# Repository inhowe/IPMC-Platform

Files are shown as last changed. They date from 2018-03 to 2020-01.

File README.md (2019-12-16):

# IPMC测控平台-NUAA-IBSS

版本索取API：https://api.github.com/repos/drinow/IPMC-Platform/releases/latest

## 更新日志
- 20191216更新
  - 发现BUG，关闭了采样率调整功能
  - 输出电流过大时，系统执行自动复位
- 20190515更新
	- 现在可以在升级前知道新版本具体更新了哪些东西
	- 新增分隔显示的曲线图
	- 控制功能统一移入到选项卡中
	- 完善上位机和下位机的功率控制算法，现已支持功率补偿
	- 其他细节优化，使逻辑性更加统一，结构更加高效
- 20190513更新
	- 增大曲线能够存储的点数（400W点）
	- 给XY图增加一个使能开关，默认关闭
- 20190509更新
	- 新增更新控制参数按钮
- 20190506更新
	- 上位机降低XY图的数据量，新增"清空XY图"按键，现在因XY图数据量过大出现卡顿现象的概率更低了
	- 上位机修改了"使能控制"按钮逻辑，你的每一次操作都能被正确反映
	- 上位机现在支持访问github从而下载完整工程了
	- 下位机新增IIR、RC滤波器，信号噪声现得到了有效抑制
	- 其他的细节优化
- 20190412更新
    - 上位机新增电路原理图、BOM单等资料
    - 测控板新增独立看门狗程序
- 20190406更新
    - 新增许多说明资料以及TIPS提示框
    - 修改了更新URL
    - 新增LICENCE
    - 其他优化
- 20190316更新
    - 新增PID等控制功能
    - 界面降级并优化
    - 细节修复
- 20190305更新
    - 新增PID控制、BangBang控制功能及界面
    - BUG修复
    - 新增协议，包括支持开关DEBUG模式、开关控制模式、系统复位等功能
    - 过流、过压等超量程指示灯改为红色
- 20180915更新
	- 修改界面为NXP风格（需要使用最新的LabView驱动）
- 20180912更新
	- 新增XY图
	- 新增提示消息
	- 新增一些功能开关
	- 优化部分逻辑
- 20180714更新
	- 提高串口速率至460800，提高采样率至10ms；
	- 修改上位机相应解析代码；
	- 替换掉RS485芯片，以与机械臂通信；
- 20180709更新
	- 增加了双通道同时控制的支持；
- 20180609更新
	- 硬件上提高了力传感器放大倍数；
	- 增加了过流状态下（1A）的LED指示；
	- 降低了ADC采样速度，以提高检测精度；
- 20180526更新
	- 提高了图表缓冲区大小，新增图表开关，新增采样时间选项，解决长时间运行后程序卡顿问题；
	- 增加温湿度传感器，及其解析；
- 20180525更新
	- 修改上位机协议解析函数，提高了解析准确度；
- 20180519更新
	- 上位机支持波形显示等相关功能；
- 20180518更新
	- 新增简单的ADC归零程序，电压完成校准；
	- 新增自定义ftoa函数，格式化输出；
	- 调整上位机显示界面，增加版本号显示（“关于”按钮）；
	- 上位机新增快捷键支持；
- 20180516更新
	- 新增激光位移传感器检测；
	- 新增错误码指示，LED快闪表示出现错误；
- 20180511更新
	- 上位机增加自动获取管理员权限功能；
	- 修正了多次安装后在应用程序删除列表下可能出现的多个应用的问题；
- 20180506更新
	- 上位机支持自动更新；
- 20180505更新
	- 移植UCOS-II，无操作系统的版本暂不更新；
	- 支持检测版本更新，但尚不支持进行版本更新；
- 20180501更新
	- 新添了自动搜寻串口功能；
	- 细节优化；
- 20180430更新
	- 调通了CAN总线；
	- 增加了上位机；
	- 支持通过CAN总线完成两个板子的级联控制，通过KEY按钮切换板子编号（红、蓝灯）；
	- 标注了原理图缺陷之处；
- 20180312更新
	- 发布第一代PCB；
	- 添加README；
	- 等待PCB测试...；
- 20180407更新
	- 注释了PCB的缺陷之处；
	- 调通DAC和ADC；

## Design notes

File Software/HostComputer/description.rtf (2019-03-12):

1. ”IPMC.exe”为主体程序，可以单独运行；
2. ”launch.exe”为更新检测程序，完成IPMC.exe的自动更新；
3. GitHub因国内网络问题可能访问较慢，导致更新失败；
4. 本工程相关代码参阅：https://github.com/drinow/IPMC-Platform/releases
5. 手动更新文件：
① 访问上述链接，下载最新IPMC.zip文件
② 解压IPMC.zip到安装目录（如“C:\Program Files (x86)\IPMC-Platform“）
③ 修改version.ini内的版本号与网站最新Tags号一致（如number=“0.3”修改为number=“0.4”）
6. 激光位移传感器的通信速率是115200bps，该传感器的默认速率是9600。如若重置激光传感器，将可能导致位移通信失败，请检查传感器的通信速率！
7. 测控平台供电电压请务必严格遵守，不可随意修改。

免责声明：作者不对该软件可能导致的任何问题负责。
�2018-现在 INHOWE IBSS,NUAA

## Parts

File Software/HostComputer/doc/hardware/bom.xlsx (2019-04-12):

Comment | Description | Designator | Footprint | LibRef | Quantity
AD5722 | 双极性DAC | *1 | TSSOP24P | AD5722 | 1
LM336Z2.5 | 基准电压芯片2.5/5V | *2, *6, *7, *8 | TO-92A | LM336 | 4
OPA564AIDWP | PAD on Bottom | *3, *4 | HSOP20 | OPA564AIDWP | 2
ADS1115IDGSR | 模数转换器 | *9 | MSOP-UN10_N | ADS1115 | 1
SHT20 | 温湿度传感器 | *10 | DFN6 | SHT20 | 1
100nF | 贴片电容 | C1, C2, C3, C4, C5, C6, C7, C8, C12, C13, C16, C17, C19, C20, C23, C27, C29, C30, C31, C32, C33, C34, C35, C36, C37, C38, C39, C42, C43, C44, C49, C50, C51, C52, C53, C54 | 0805_C | 0805 100nF(104) 10% 50V | 36
470uF/35V | 贴片铝电解电容 | C9, C21 | 10*10mm | Cap Pol | 2
47uF/35V | 贴片铝电解电容 | C10, C11, C14, C15 | 6*5mm | Cap Pol | 4
220uF/16V | 贴片铝电解电容 | C18, C22 | 6*5mm | Cap Pol | 2
1nF | 贴片电容 | C24, C25 | 0805_C | 0805 1nF (102) 10% 50V | 2
10uF | 贴片电容 | C26, C28 | 0805_C | 0805 10uF (106) 10% 25V | 2
2.2uF | 贴片电容 | C40, C41 | 0805_C | 0805 2.2uF (225) 20% 50V | 2
22pF | 贴片电容 | C45, C46, C47, C48 | 0805_C | 0805 22pF (220) 5% 50V | 4
Header 2 | 2.54mm接插件2pin | CAN1, DA0, DA1 | HDR2X1_B1 | Header 2 | 3
SS54(1N5824) | 二极管 | D1, D4 | DIODE-SMA | Diode | 2
ZM4732 | 稳压二极管 | D5, D6 | LL-41 | Diode-Z | 2
1N4001 | 二极管(1N4001)贴片形式 | D7, D8 | DIODE-SMA | Diode | 2
KF301-3P | 蓝色电源端子 | DC | KF301-3P | KF301-3P | 1
Header 4 | Header, 4-Pin | Force Sensor | HDR4X1_B1 | Header 4 | 1
SW-PB | 3mm*6mm轻触开关 | KEY, RESET | 3*6mm | SW-PB | 2
CDRH127-33uH | 功率电感 | L1, L2 | L-SMD-12 | Inductor | 2
10uH/磁珠 | 贴片电感 | L3 | 0805_L | 0805 10uH 10% | 1
10uH | 贴片电感 | L4 | 0805_L | 0805 10uH 10% | 1
红灯 0805 | 发光二极管 | LED0, PWR | 0805_LED_S1 | 0805 红灯 | 2
翠绿 0805 | 发光二极管 | LED1 | 0805_LED_S1 | 0805 翠绿 | 1
120Ω | 贴片电阻 | R1, R28 | 0805_R | 0805 120Ω (1200) 1% | 2
2.4KΩ | 贴片电阻 | R2, R18, R19, R20 | 0805_R | 0805 2.4KΩ (2401) 1% | 4
1KΩ | 贴片电阻 | R3, R4, R12, R15, R24 | 0805_R | 0805 1KΩ (1001) 1%, 0805 20KΩ (2002) 1% | 5
10KΩ | 贴片电阻 | R5, R6, R8, R9, R10, R11, R26, R27 | 0805_R | 0805 10KΩ (1002) 1%, 0805 20KΩ (2002) 1% | 8
10mR | 贴片电阻 | R7 | 2512 | Res1 | 1
0Ω | 贴片电阻 | R13 | 0805_R | 0805 0Ω (0R0) 1% | 1
200Ω | 贴片电阻 | R14 | 0805_R | 0805 200Ω (2000) 1% | 1
4.7KΩ | 贴片电阻 | R16, R17, R21, R22, R23, R25 | 0805_R | 0805 4.7KΩ (4701) 1% | 6
RJ11-6P6C | RJ11电话插座 | RS232 | RJ6-RJ11 | RJ11 | 1
Header 3 | 2.54mm接插件3pin | RS485 | HDR3X1_B1 | Header 3 | 1
Header 4 | 2.54mm接插件4pin | SWD | HDR1X4 | Header 4 | 1
M3铜柱螺丝 |  | T1, T2, T3, T4 | 螺丝孔-3MM | M3铜柱螺丝孔 | 4
SP3232EEY-L/TR | RS232 | U1 | TSSOP-16 | SP3232EEY-L/TR | 1
SP3485EN-L/TR | RS-485/RS-422 | U2 | SOIC-8_150MIL | SP3485EN-L/TR | 1
LM2596S-5.0 | 5V稳压芯片 | U3, U4 | TO263-5 | LM2596S-5.0 | 2
STM32F405RGT6 | ARM Cortex-M4 32-bit MCU+FPU, 210 DMIPS, 1024 kB Flash, 192 kB Internal RAM, 51 I/Os, 64-pin LQFP, -40 to 85 degC, Tray | U5 | STM-LQFP64_L | STM32F405RGT6 | 1
AD620ARZ-REEL | 仪放 | U6, U7, U8 | SOIC-8_150MIL | AD620ARZ-REEL | 3
CH340G | USB转串口芯片（江苏沁恒公司） | U9 | SOIC-16_150MIL | CH340G | 1
TJA1050T/CM | CAN | U10 | SOIC-8_150MIL | CAN/TJA1050T/CM | 1
MicroUSB母座 | MicroUSB贴片母座，MK5P，带固定柱，针长1.35mm | USART | USB_MICRO | USB_M | 1
AMS1117-3.3 | 低压差线性稳压(LDO) | VR1 | SOT223 | SOT-223 AMS1117-3.3 | 1
12MHZ | 无源贴片晶振 | Y1 | SMD-3225_4P | SMD-3225_4P 12MHZ 20PF 10PPM | 1
25MHZ | 无源贴片晶振 | Y2 | SMD-3225_4P | SMD-3225_4P 25MHZ 12PF 10PPM | 1

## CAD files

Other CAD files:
Storage/平台外壳.dwg

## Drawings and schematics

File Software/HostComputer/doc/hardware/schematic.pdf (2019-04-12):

RS232

## Communication Interface

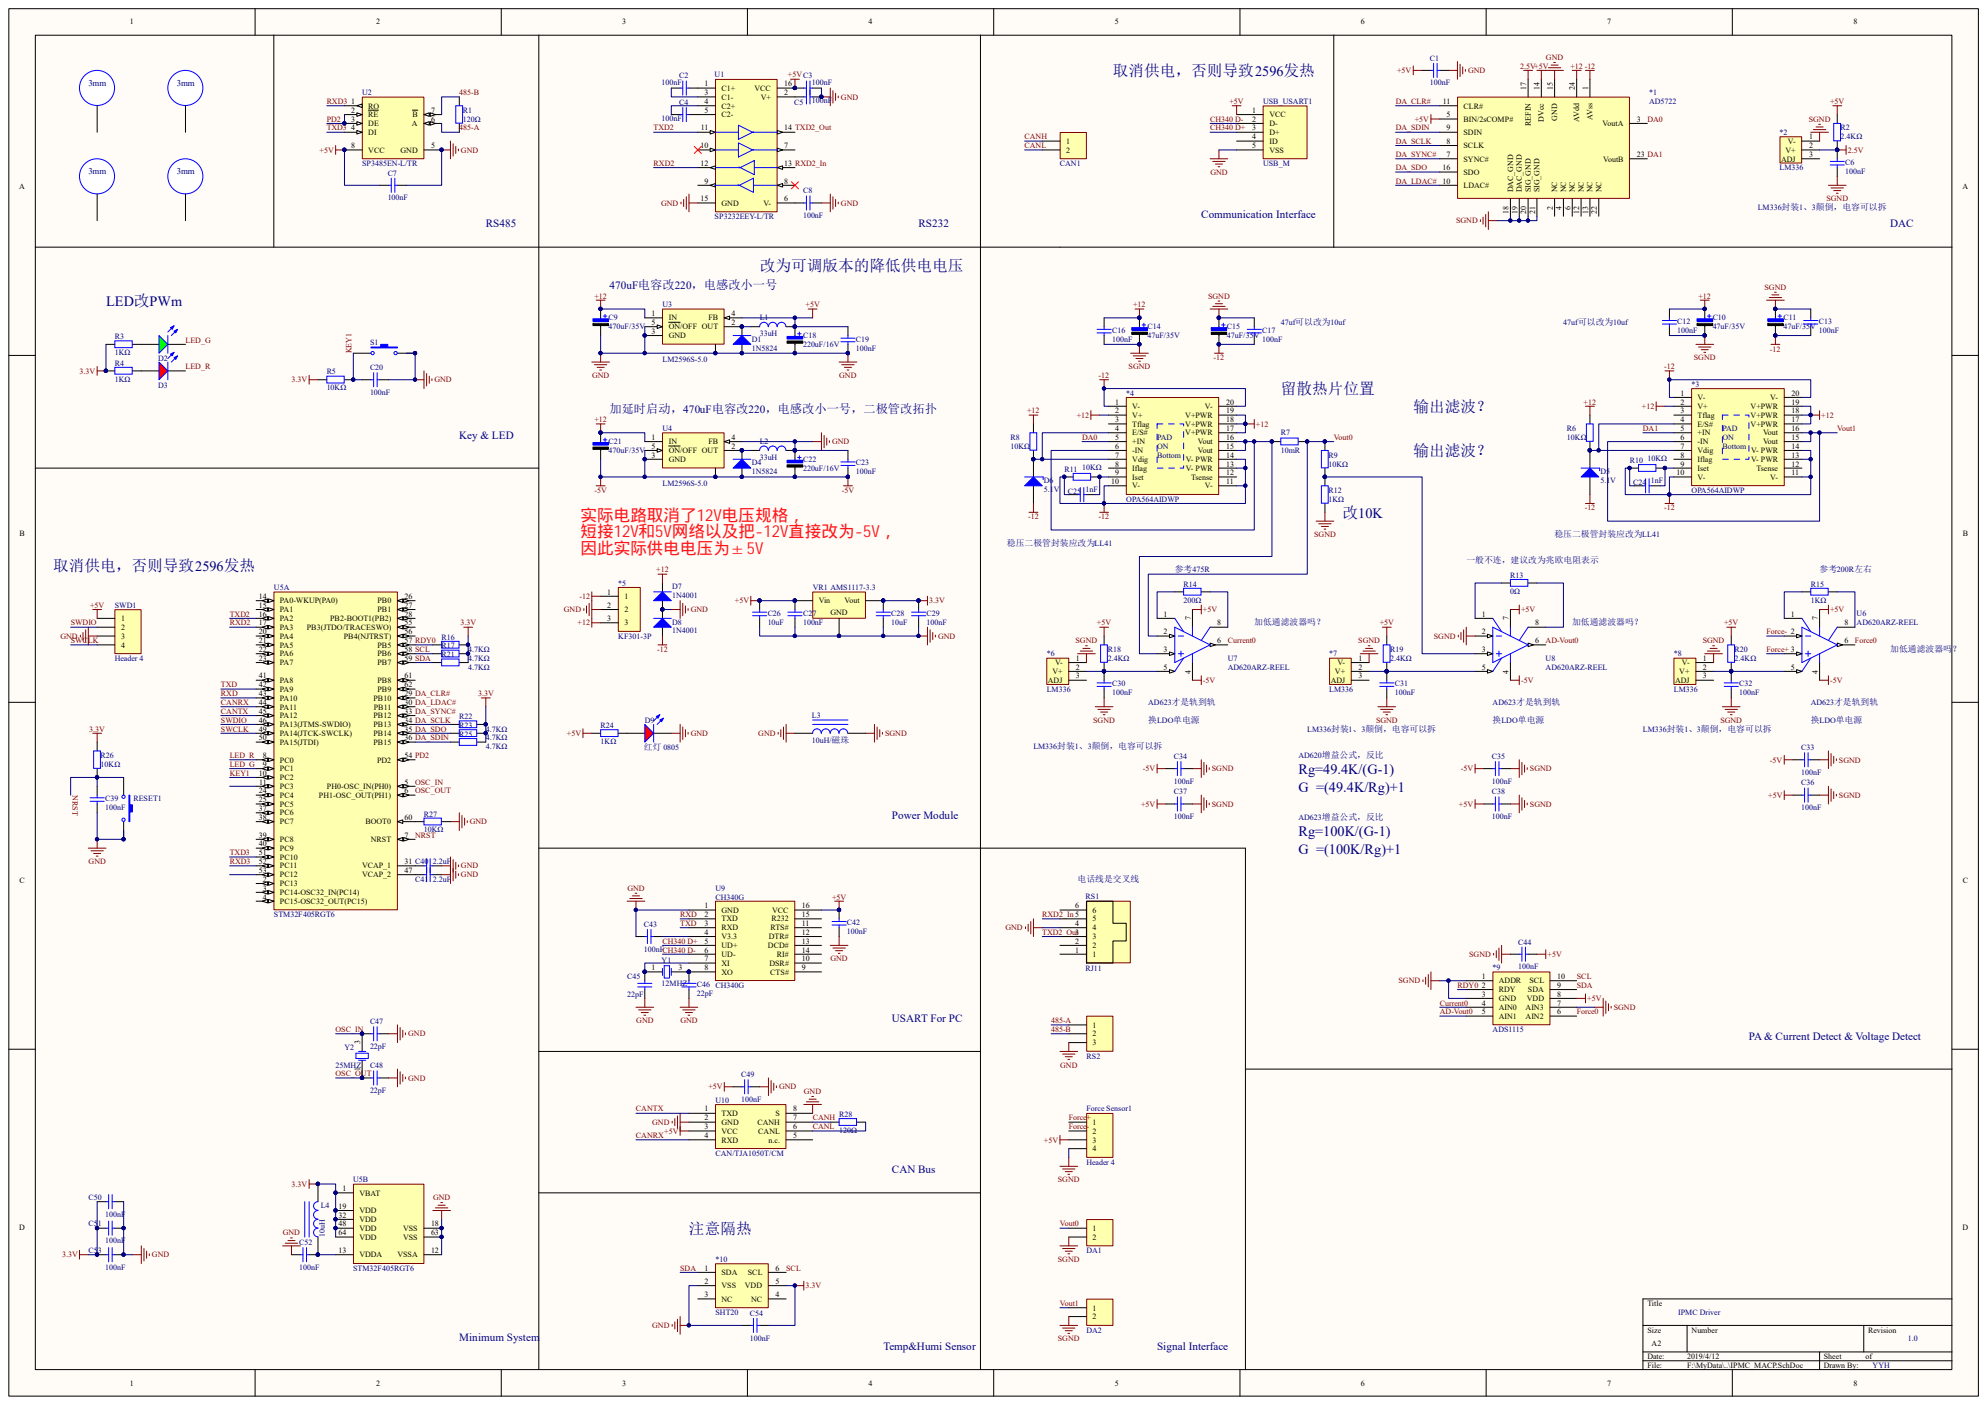
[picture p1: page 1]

PA & Current Detect & Voltage Detect

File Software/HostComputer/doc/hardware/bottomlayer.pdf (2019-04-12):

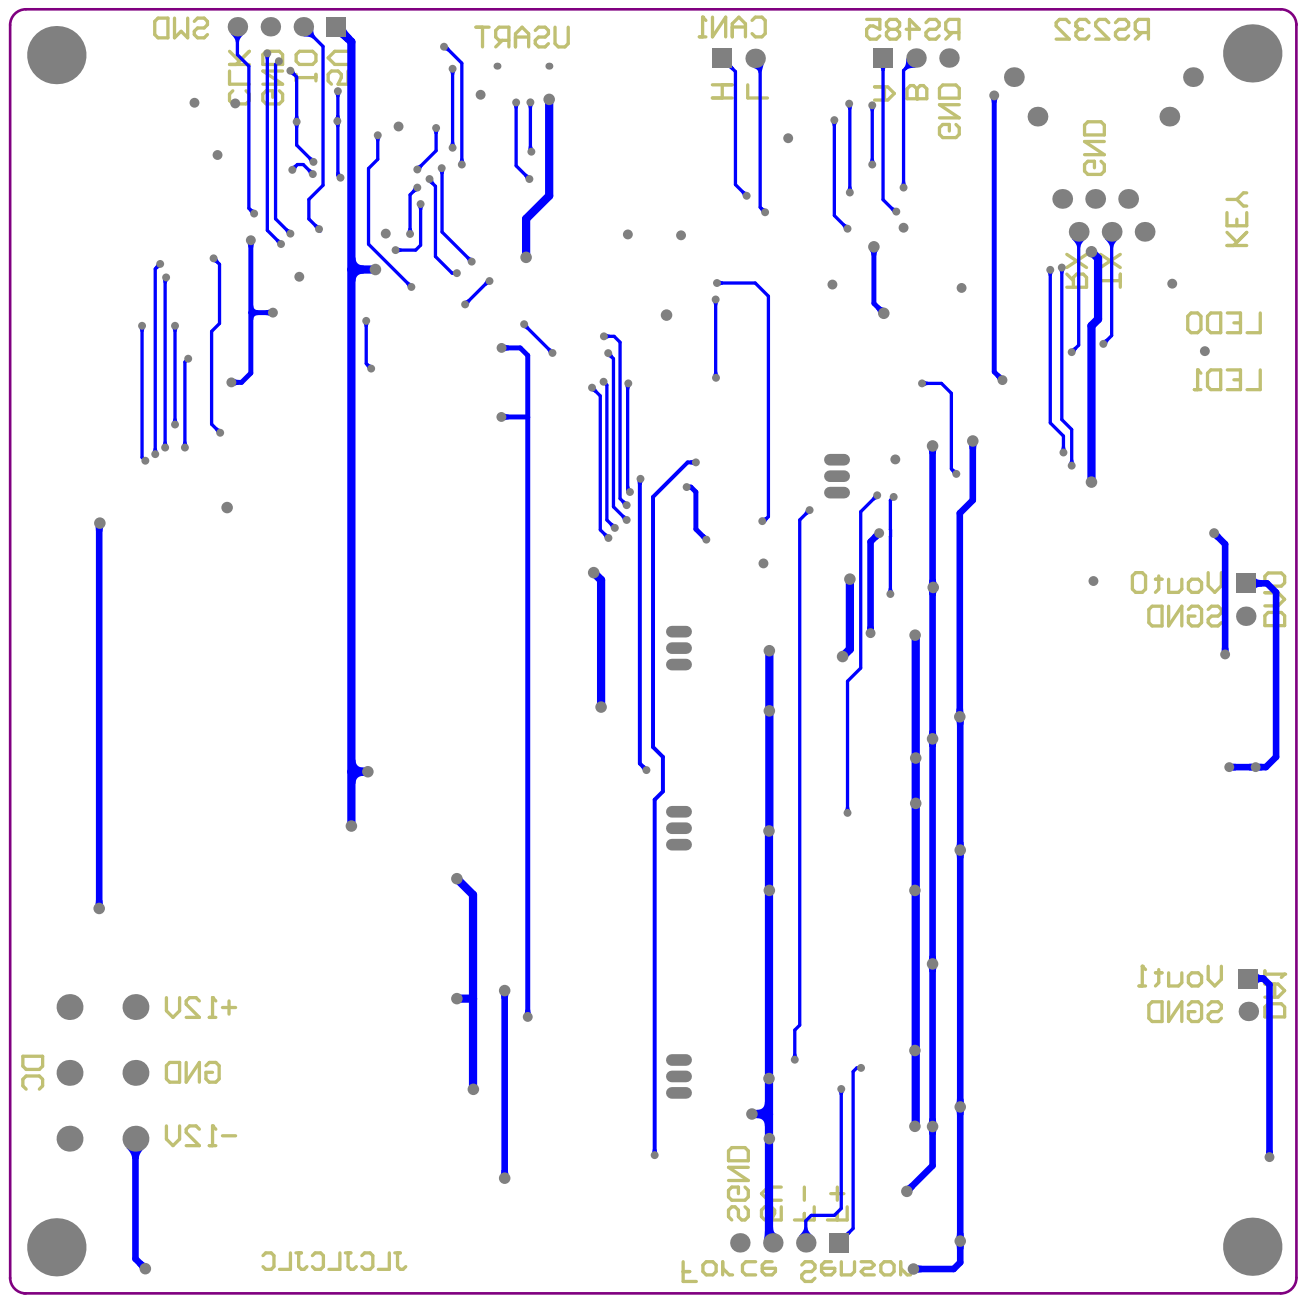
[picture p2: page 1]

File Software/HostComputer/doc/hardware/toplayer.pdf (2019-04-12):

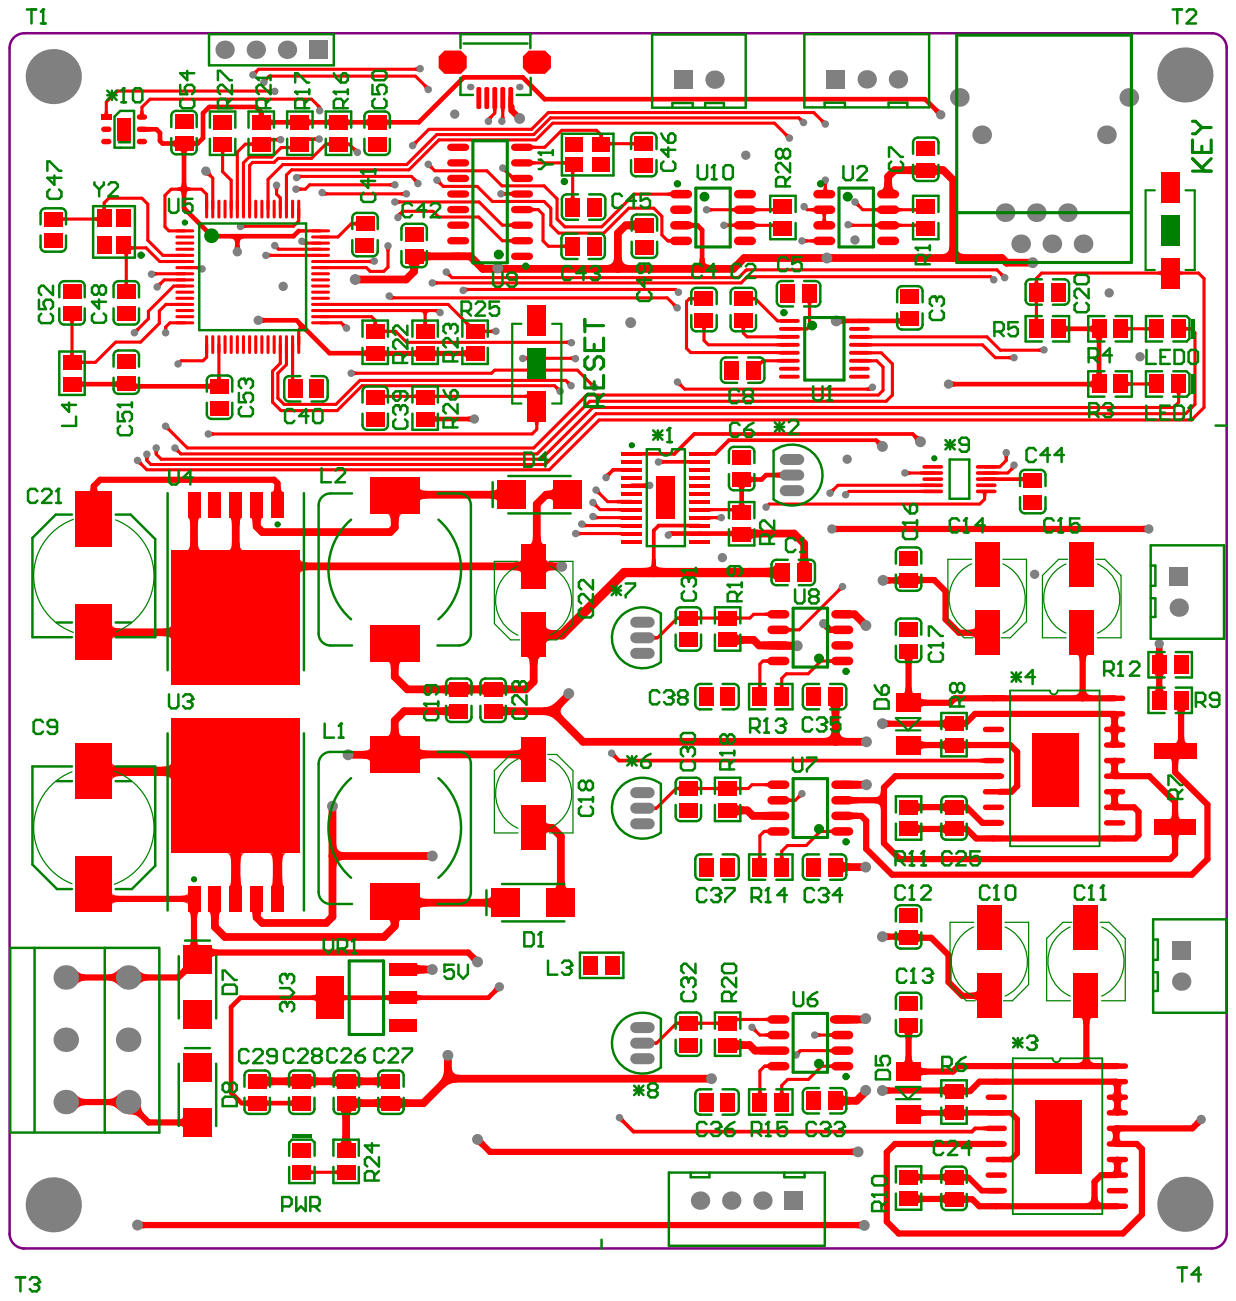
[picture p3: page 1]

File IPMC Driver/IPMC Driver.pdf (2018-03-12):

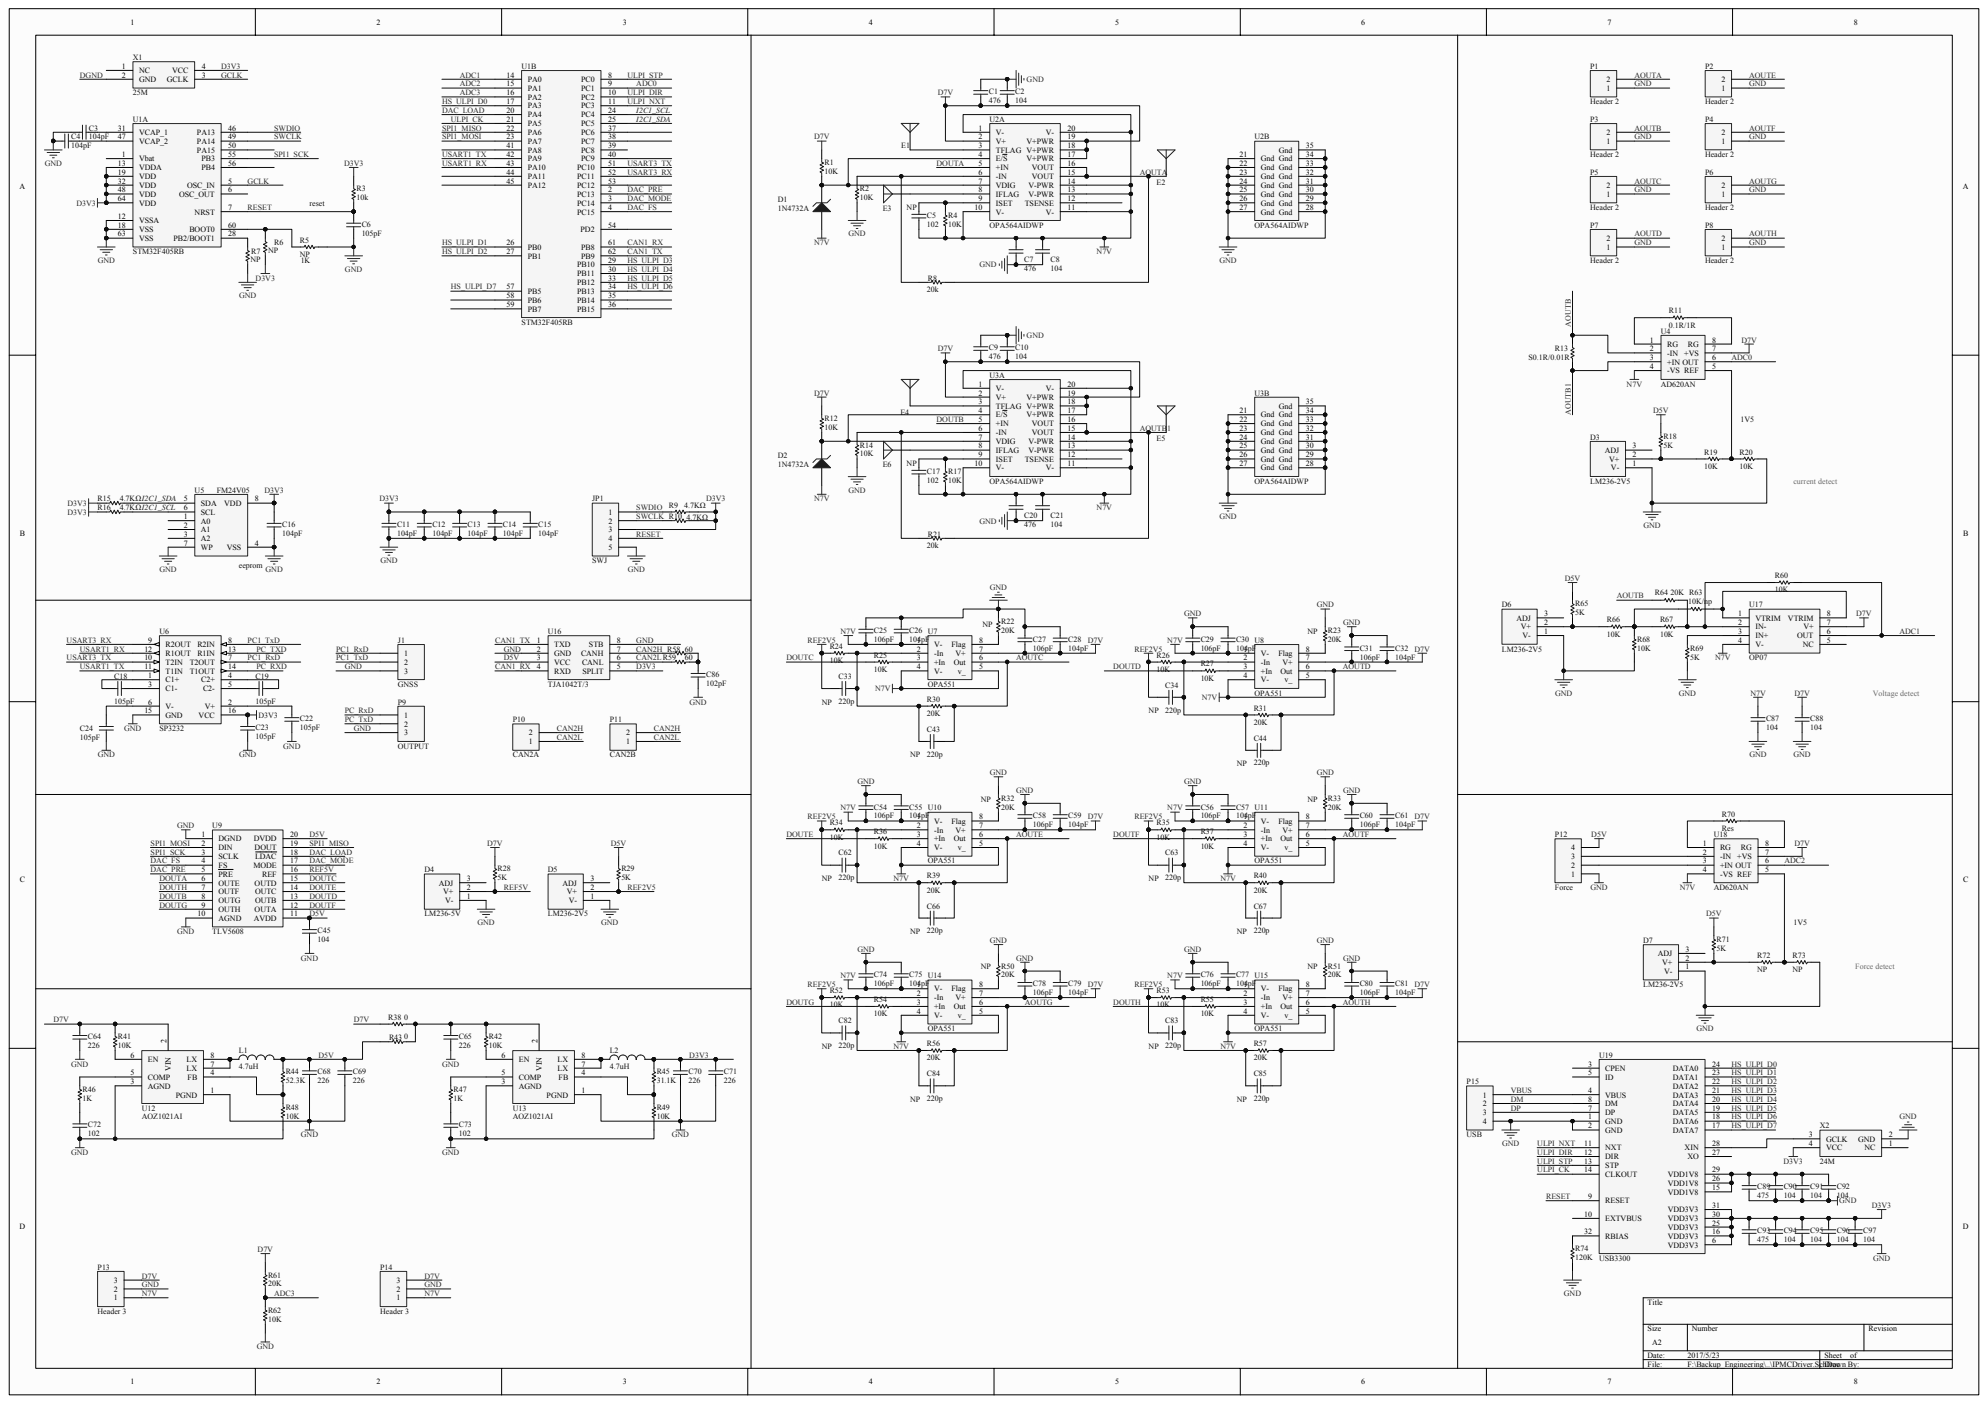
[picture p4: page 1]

AOUTB1 AOUTB RG 1 -IN 2 +IN 3 -VS 4 REF 5 OUT 6 +VS 7 RG 8 U4 AD620AN 0.1R/1R R11 N7V D7V ADC0

Size A2 | Number | Revision

Date: 2017/5/23 | Sheet of
File: F:\Backup_Engineering\..\IPMCDriver.SchDoc Drawn By:

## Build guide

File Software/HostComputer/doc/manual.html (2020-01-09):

# IPMC测控平台使用手册

概念定义：
上位机=测控平台=电脑上所运行的IPMC-Platform程序；
下位机=测控板=电路板及其该电路板上所运行的程序；

## 1.电路板使用说明

### 1.1接口说明

灯光：

- 电源灯：常亮红色灯；
- 蓝色灯：
  - 慢闪1下----程序运行正常；
  - 连闪2下----激光位移传感器通信失败；
- 红色灯：亮起----电流传感器接近满量程/力传感器接近满量程；

颜色--板子编号（蓝LED0、红LED1）；
板子编号：

- 蓝灯作为闪烁灯----0号电路板；
- 红灯作为闪烁灯----1号电路板；

当电路板编号改变时，上述红蓝灯的含义互换。

按键：
KEY键（位于边缘）：切换板子编号，切换编号后，红蓝灯含义互换，原来蓝灯闪烁表示的含义由红灯闪烁代替。
RESET键（位于中间）：系统复位。

USB口：
用于和电脑连接。

CAN口：
用于多电路板连接，CANH连CANH，CANL连CANL，并保证闪烁的灯颜色不一致。

RJ11口（RS232）：
用于和激光位移传感器KEYENCE LKGD500连接。

### 1.2如何供电

- 电路板的供电电压为±5V。
- 从常亮的红色电源指示灯侧起，分别是-5V，GND，+5V。
- 不可以接错也不可以使用其他规格的电压，否则可能导致设备损坏。

### 1.3抗干扰措施

- 测控板所处环境应该具有干净的电磁环境，应该远离各类射频设备或者非金属外壳的电源设备，尤其是无线路由器、手机等设备。
- 应使用带有屏蔽线缆的力传感器。
- 使用实验室的直流可调电源具有优良的纹波特性(<2mVrms)，用它供电可以有效提高力传感器的测量精度。由于该电源开机立刻供电，因此在连接电缆前应确保可调电源设置的电压规格符合测控板要求。

### 1.4如何重刷固件

警告：该操作非常危险，如若失败将会导致系统变砖，若固件没有致命故障禁止尝试。

1. 持续按住测控板上的KEY键，插上供电线缆（或单击上位机的"复位系统"按钮）。
2. 测控板上两枚LED将会快速闪烁，持续按住直到不再闪烁(约2.5秒)
3. 松开按键，此时测控板进入Recovery模式。
4. 确认测控平台选择的端口号正确，点击Recovery模式，并点击确定，系统将会擦除原有固件并写入新固件。
5. 耐心等待写入完成，如若写入成功，系统会自动进入正常工作模式，可通过LED是否闪烁来简单判断。
6. 如果写入失败，切勿断电，请直接重复步骤4。

系统变砖挽救办法：

1. 断开所有线缆，确保测控板未供电。
2. 寻找一根导线，用于短接3.3V电源焊点与R27电阻靠近STM32侧的焊点。(3.3V电源在红色电源灯附近有标注，R27电阻在STM32附近。)
3. 插上电缆，此时测控板进入Recovery模式
4. 确认测控平台选择的端口号正确，点击Recovery模式，并点击确定，系统将会擦除原有固件并写入新固件。
5. 耐心等待写入完成，如若写入成功，系统会自动进入正常工作模式，可通过LED是否闪烁来简单判断。
6. 如果写入失败，切勿断电，请直接重复步骤4。

固件文件存放相对路径:"./doc/software/firmware/IPMC.hex"

## 2.上位机使用说明

### 2.1如何保存数据

右键曲线框----导出----选择导出的文件格式即可。
导出的数据范围取决于曲线坐标轴，请确保曲线框的标尺覆盖了所需的数据范围，如果没有，请调节坐标轴。
导出的数据会导出所有数据，无需显示所有曲线，只需要确认数据范围是标尺范围的子集即可。

### 2.2如何显示/关闭曲线

单击右侧图例，即可显示/关闭曲线，该操作只是显示功能的开关，数据依然会在内存中记录。

### 2.3如何打开/关闭曲线图表

该功能由复选框控制，位于曲线图表右侧，与2.2不同的是，该操作将会停止波形的记录，但是不影响波形输出也不影响下方的数据显示框。

### 2.4如何调节坐标轴

点击图表右侧的工具选板的放大镜按钮，即可选择不同的模式对坐标轴放大或者缩小。

### 2.5如何关闭坐标轴自动调节

右键曲线框----关闭自动调节X/Y标尺。
双击坐标轴两侧端点的数字，即可进行编辑，退出编辑即完成坐标轴的调节。

### 2.6如何自动测量

勾选“自动测量按钮”，此时“时长 S”选项框可以进行编辑。
选择好需要输出的波形，以及你需要测量的时长。S
点击“发送波形”，即可自动输出波形并测量，同时倒计时结束时停止信号输出。

### 2.7如何清空图表

单击“清空图表”按钮即可清空图表并重置坐标轴。
右击图表，选择“清除图表”，即可清除图表但不重置坐标轴。
点击“发送波形”，即可自动输出波形并测量，同时倒计时结束时停止信号输出。

### 2.8如何降低采样频率以减少数据量

目前无法直接降低采样频率，可以通过把导出的数据每隔n行选一行来间接的降低采样频率。
参考链接：Excel每隔几行选择一行的小技巧 (https://jingyan.baidu.com/article/76a7e409101598fc3b6e15bd.html)

### 2.9文档目录树说明

- "./stm32isp.exe"该文件用于重刷测控板固件
- "./stm32isplog.txt"该文件是stm32isp.exe的log记录文件
- "./download.exe"该文件用于下载上位机更新文件
- "./launch.exe"该文件是测控平台启动文件，用于检查更新和替换上位机文件
- "./IPMC.exe"该文件是测控平台主程序文件
- "./driver/"该目录存放的是USB转串口驱动文件
- "./doc/sourcecode.html"打开该文件可以下载工程源码
- "./doc/description.rtf"该文件是描述文件
- "./doc/license.rtf"该文件是软件分发许可证书文件
- "./doc/manual.html"该文件是软件使用手册
- "./doc/protocol.xlxs"该文件是测控平台（上位机）和测控板（下位机）的通讯协议文件
- "./doc/hardware/"该目录存放测控板硬件资料，包括工程文件、原理图、bom单等
- "./doc/software/"该目录存放测控板软件资料，包括工程文件、已编译固件等

## 3.快速故障排查

### 3.1激光传感器无数据

- 检查接线是否松动，重新插拔，等待10秒钟，看是否有数据；
- 检查激光传感器通信率是否为115200。 传感器设置方法：
  1. 长按SET（HEAD-A闪烁）；
  2. 按5下↑键（Enu闪烁）；
  3. 按2下ENT（A-Bx闪烁,x为某数字）；
  4. 检查红色数字是否为115200，如果不是，按↑键调出115200；
  5. 按1下ENT键保存当前配置
  6. 重复按SET键，逐级退出，直到显示出现位移为止。

### 3.2测试夹无输出/输出异常

- 设置1~2V的输出电压，短暂的闭合夹子（1秒），使输出短路，测控板是否会亮红灯
  - 不亮：用万用表检测DA口电压是否和预设一致。 一致：接触不良。 不一致：电路板故障。
  - 有时亮：可能是接触不良，尝试更换夹子电极，并给夹子捆绑橡皮筋增加接触力。
- 是否忘记对系统进行双电源供电？

### 3.3力传感器数据异常

- 是否超量程（红灯亮起）
- 应使用直流可调电源。
- 应避免震动。
- 应避免风。

### 3.4电流传感器数据异常

- 是否超量程（红灯亮起）
- 输出电压不应高于3.5V。
- 旁边是否有功率射频设备？如无线路由器、通话中的手机。

### 3.5上位机无数据

- 波特率应为460800。
- 端口号是否正确？在设备管理器中看看
- 误码灯点亮：尝试重新连接
- 勾选“显示图表”
- 取消勾选后台状态----调试模式

最后更新日期：20191216
免责声明：作者对本软件造成的任何影响不承担任何责任
© 2018-现在 INHOWE, IBSS, NUAA
源代码： https://github.com/inhowe/IPMC-Platform

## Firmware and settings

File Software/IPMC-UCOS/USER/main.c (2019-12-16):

#include "sys.h"
#include "includes.h"
/************************************************
 *作者：@inhowe 
************************************************/
static void MX_NVIC_Init(void);
static void BSP_Init(void);

#define VERSION     0x10//固件版本

//用户配置变量的FLASH地址
#define USR_CONFIG_ADDR     ((uint32_t)0x08080000)

OS_EVENT * CAN_Q;
OS_EVENT * UART1_Q;
OS_EVENT * COM2Msg;
void*   CAN_QTbl[64];
void* UART1_QTbl[64];

float TEMP=0,HUMI=0;
/*
ErrCode Bit Description
Reference @ErrCodeBitDefine
*/
INT16U ErrCode=0;
INT16U BoardID=0x00;

bool DBG_Flag=false;
bool CTR_Flag=false;
bool CARLIB_OK_Flag=false;

double Current_mA=0,Power_mW=0,Force_mN=0,Energy_mJ=0,Laser_mm=0,dLaser_mm=0;

//DEBUG时应关闭IWDG，可在Peripheral-DBG寄存器里勾选DBG_IWDEG_STOP
int main(void)
{
	HAL_Init();                     //初始化HAL库   
	Stm32_Clock_Init(336,25,2,8);   //设置时钟,168Mhz
	delay_init(168);                //初始化延时函数
	BSP_Init();
	
	OSInit();                       //UCOS初始化，重置用到的变量、建立空闲任务、建立统计任务等
    
	UART1_Q = OSQCreate(&UART1_QTbl[0],64);
	CAN_Q   = OSQCreate(&CAN_QTbl[0],64);
	COM2Msg = OSMboxCreate((void *)0);

	OSTaskCreateExt((void(*)(void*) )start_task,                //任务函数
									(void*          )0,                         //传递给任务函数的参数
									(OS_STK*        )&START_TASK_STK[START_STK_SIZE-1],//任务堆栈栈顶
									(INT8U          )START_TASK_PRIO,           //任务优先级
									(INT16U         )START_TASK_PRIO,           //任务ID，这里设置为和优先级一样
									(OS_STK*        )&START_TASK_STK[0],        //任务堆栈栈底
									(INT32U         )START_STK_SIZE,            //任务堆栈大小
									(void*          )0,                         //用户补充的存储区
									(INT16U         )OS_TASK_OPT_STK_CHK|OS_TASK_OPT_STK_CLR|OS_TASK_OPT_SAVE_FP);//任务选项,为了保险起见，所有任务都保存浮点寄存器的值
	OSStart(); //开始任务
}

static void BSP_Init(void)
{
    uint16_t cnt=0;
    
	MX_NVIC_Init();
	
    uart1_init(460800);//USART
    uart2_init(115200);//RS232
    LED_Init();                     //初始化LED
    KeyInit();

    #ifdef ROBOT_ARM
        IPMC_Init();
    #else
        uart3_init(115200);//RS485
    #endif
    if(DBG_Flag==false)
        MYDMA_Config(DMA2_Stream7,DMA_CHANNEL_4);//初始化DMA

    IIC_Init();
    CAN1_Mode_Init(CAN_SJW_1TQ,CAN_BS2_6TQ,CAN_BS1_8TQ,6,CAN_MODE_NORMAL); //CAN初始化,波特率500Kbps      
    AD5722_Init();
    Channel_Group_Init();	
    SHT2x_Init();
    LaserCMDToZero();
    Queue_Init(&UART_RXqueue);
    Queue_Init(&CAN_RXqueue);
    
    cnt=0;
    while(HAL_GPIO_ReadPin(KEY_GPIO_Port,KEY_Pin)==GPIO_PIN_RESET )//按键启动
    {
        delay_ms(100);
        LED0=LED1=LED_ON;
        delay_ms(100);
        LED0=LED1=LED_OFF;
        cnt++;
        if(cnt>=25)break;
    }
    if(cnt>=25)
    {
        UpgradeSystem();
    }
    else if(cnt>=1)//short press
    {
        DBG_Flag=true;
//        IWDG_Init();
    }
    else
    {
        IWDG_Init();
    }
}

static void MX_NVIC_Init(void)
{
  /* TIM6_DAC_IRQn interrupt configuration */
  HAL_NVIC_SetPriority(TIM6_DAC_IRQn, 0, 0);
  HAL_NVIC_EnableIRQ(TIM6_DAC_IRQn);
  /* USART1_IRQn interrupt configuration */
  HAL_NVIC_SetPriority(USART1_IRQn, 1, 0);
  HAL_NVIC_EnableIRQ(USART1_IRQn);
  /* USART2_IRQn interrupt configuration */
  HAL_NVIC_SetPriority(USART2_IRQn, 2, 0);
  HAL_NVIC_EnableIRQ(USART2_IRQn);
  /* CAN1_RX0_IRQn interrupt configuration */
  HAL_NVIC_SetPriority(CAN1_RX0_IRQn, 3, 0);
  HAL_NVIC_EnableIRQ(CAN1_RX0_IRQn);
}

void JumpToISP(void)
{
    //ISP代码地址
    #define ISPAddress 0x1FFF0000 
    
    //程序跳转不复位外设，建议对一些可能导致问题的外设进行反初始化DeInit，如SysTick。
    //看门狗一旦初始化不能被关闭，因此如果使用了看门狗，则在调用该函数前，必须先复位系统，并在初始化看门狗之前调用该函数。
    uint32_t ispJumpAddr;//ISP程序的跳转地址，既程序入口
    uint32_t ispSpValue;//IAP程序的SP初值，即栈指针
    void (*Jump_To_ISP)(void);//定义一个函数指针
    
    SysTick->CTRL=0x00;       //关闭计数器
    SysTick->VAL =0X00;       //清空计数器	

    if (((*(__IO uint32_t*)ISPAddress) & 0x2FFE0000 ) == 0x20000000)
    { 
        ispSpValue  = *(__IO uint32_t*)ISPAddress;
        ispJumpAddr = *(__IO uint32_t*)(ISPAddress+4);


        /* 初始化 Stack Pointer */
        __set_MSP(ispSpValue);

        /* Jump to isp */
        Jump_To_ISP = (void (*)(void))ispJumpAddr;
        Jump_To_ISP();
    }
}

void UpgradeSystem(void)
{
    LED0=LED1=LED_ON;
    printf("\r\nPlease release your COM port, and call the stm32isp.exe.");
    printf("\r\nEntering booloader...");
    JumpToISP();
}

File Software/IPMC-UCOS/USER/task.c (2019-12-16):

#include "task.h"

__align(8) OS_STK LED_TASK_STK[LED_STK_SIZE];
__align(8) OS_STK DAC_TASK_STK[DAC_STK_SIZE];
__align(8) OS_STK ADC_TASK_STK[ADC_STK_SIZE];
__align(8) OS_STK COM_TASK_STK[COM_STK_SIZE];
__align(8) OS_STK PRINT_TASK_STK[PRINT_STK_SIZE];
__align(8) OS_STK START_TASK_STK[START_STK_SIZE];
__align(8) OS_STK IDLE_TASK_STK[IDLE_STK_SIZE];
__align(8) OS_STK LASER_TASK_STK[LASER_STK_SIZE];
__align(8) OS_STK SHT20_TASK_STK[SHT20_STK_SIZE];

//LED0任务
void led_task(void *pdata)
{
    #define SHORT_DELAY 120
    //0是亮
    INT8U time=1,i=0;
    while(1)
    {
        IWDG_Feed();
        for(i=0;i<time;i++)
        {
            if(BoardID==0x00)
            {	
                LED0=LED_ON;
                if(ReadBit(ErrCode,OverForceBIT)||ReadBit(ErrCode,OverCurrentBIT))
                    LED1=LED_ON;
                else
                    LED1=LED_OFF;
            }
            else
            {	LED1=LED_ON;
                if(ReadBit(ErrCode,OverForceBIT)||ReadBit(ErrCode,OverCurrentBIT))
                    LED0=LED_ON;
                else
                    LED0=LED_OFF;
            }
            delay_ms(SHORT_DELAY);
            if(BoardID==0x00)
            {	
                LED0=LED_OFF;
                if(ReadBit(ErrCode,OverForceBIT)||ReadBit(ErrCode,OverCurrentBIT))
                    LED1=LED_ON;
                else
                    LED1=LED_OFF;
            }
            else
            {	
                LED1=LED_OFF;
                if(ReadBit(ErrCode,OverForceBIT)||ReadBit(ErrCode,OverCurrentBIT))
                    LED0=LED_ON;
                else
                    LED0=LED_OFF;
            }
            delay_ms(SHORT_DELAY);
        }
        time=1;
        if(ReadBit(ErrCode,LASERErrBIT))    time=2; 

        delay_ms(1000-SHORT_DELAY*2*time);
    }
}

void idle_task(void* pdata)
{
	while(1)
	{
        delay_ms(2000);
	}
}

void sht20_task(void* pdata)
{
    OS_CPU_SR cpu_sr=0;
    float T[10],H[10];
    INT8U i=0;
    while(1)
    {
        T[i]=SHT2x_GetTempPoll();
        H[i]=SHT2x_GetHumiPoll();
        OS_ENTER_CRITICAL();
        TEMP=(T[0]+T[1]+T[2]+T[3]+T[4]+T[5]+T[6]+T[7]+T[8]+T[9])/(float)10.0;
        HUMI=(H[0]+H[1]+H[2]+H[3]+H[4]+H[5]+H[6]+H[7]+H[8]+H[9])/(float)10.0;
        OS_EXIT_CRITICAL();
        i++;
        if(i==10) i=0;
        delay_ms(50);
    }
}

void laser_task(void* pdata)
{
    INT8U err,*COM2Buff;
    INT16U time=10;
    OS_CPU_SR cpu_sr=0;
    while(1)
    {
        LaserCMDMessure();
        COM2Buff = OSMboxPend(COM2Msg,time,&err);
        if(err == OS_ERR_NONE)
        {
            OS_ENTER_CRITICAL();
            LaserBAKMessure(COM2Buff);
            OS_EXIT_CRITICAL();
            ClrBit(ErrCode,LASERErrBIT);
            time = 3;
        }
        else
        {   //通信失败时暂停发送数据等待传感器恢复
            LaserOffset=Laser_OutOfRange;
            time = 5000;
            SetBit(ErrCode,LASERErrBIT);
        }
        delay_ms(time);
    }
}

void com_task(void* pdata)
{
	while(1)
	{
		DealQueueBuff(&UART_RXqueue);
		DealQueueBuff(&CAN_RXqueue);
		TimerCheckKey();
		delay_ms(10);
	}
}


void print_task(void* pdata)
{
    char array[9]={'0','0','.','0','0','0','0'};
    char SendBuff[128]={0};
//    OS_STK_DATA UsedSTK;
    double Current_A=0,Voltage_V=0,Force_N=0;
		double f_Current_A=0,f_Voltage_V=0,f_Force_N=0,f_Laser_mm=0;
    double lastLaserOffset=0;
		char overCurrentCnt = 0;
	while(1)
	{
        Current_A = (ADS_Buff[0]-RefV[0])*0.000039934061560271849741418838615385; // 00006744402706230 0.00004097277=0.0001875/457.62100/0.01
        if(fabs(Current_A)<0.0005)
            f_Current_A = RC_LowPassFilter(Current_A,f_Current_A,1);
        else
            f_Current_A = RC_LowPassFilter(Current_A,f_Current_A,2);
//        f_Current_A = IIR_LowPassFilter2P5Hz_Current(Current_A);//
        Current_mA=f_Current_A*1000;//当前电流值
        if(Current_A>0.3||Current_A<-0.3){
					SetBit(ErrCode,OverCurrentBIT);//过流检测 安培
					overCurrentCnt++;
					if(overCurrentCnt >= 100) //1000ms过流复位
						HAL_NVIC_SystemReset();
					if(overCurrentCnt >= 20 && (Current_A>1.0||Current_A<-1.0) )
						HAL_NVIC_SystemReset();
				}
        else{
					ClrBit(ErrCode,OverCurrentBIT);
					overCurrentCnt = 0;
				}
        
        Voltage_V = (ADS_Buff[1]-RefV[1])*0.000374849265;//0.000375*99.959804%
        f_Voltage_V = RC_LowPassFilter(Voltage_V,f_Voltage_V,5);
        if(Current_mA>=0&&f_Voltage_V>=0)//功率不分正负但是功率有方向
            Power_mW=f_Voltage_V * Current_mA;// V*mA=mW!
        else
            Power_mW=-1*f_Voltage_V * Current_mA;
        
        Energy_mJ+=Power_mW*0.01;//能量积分，mJ
        if(ADS_Buff[1]>24000||ADS_Buff[1]<2666) SetBit(ErrCode,OverValtageBIT); //ADC绝对值高于4.5V和低于0.5V警告
        else ClrBit(ErrCode,OverValtageBIT);
    
        Force_N = 0.94019608*(-0.00022466+0.0000343215*(ADS_Buff[2]-RefV[2])-0.00000000200793*(ADS_Buff[2]-RefV[2])*(ADS_Buff[2]-RefV[2]));//2次曲线*修正系数
        if(fabs(Force_N)<0.001)
            f_Force_N = RC_LowPassFilter(Force_N,f_Force_N,0.5);
        else
            f_Force_N = RC_LowPassFilter(Force_N,f_Force_N,1);
        Force_mN = f_Force_N*1000;
        if(ADS_Buff[2]>24000||ADS_Buff[2]<2666) SetBit(ErrCode,OverForceBIT); //ADC绝对值高于4.5V和低于0.5V警告
        else ClrBit(ErrCode,OverForceBIT);
        
				if(Laser_mm!=Laser_OutOfRange)
				{
					Laser_mm = RC_LowPassFilter(LaserOffset,Laser_mm,5);
					dLaser_mm=RC_LowPassFilter(Laser_mm-lastLaserOffset,dLaser_mm,5);
					lastLaserOffset=LaserOffset;
					f_Laser_mm=Laser_mm;
				}
				
        if(__HAL_DMA_GET_FLAG(&UART1TxDMA_Handler,DMA_FLAG_TCIF3_7))//判断上次DMA2_Steam7传输完成
        {
            //清除DMA2_Steam7传输完成标志
            __HAL_DMA_CLEAR_FLAG(&UART1TxDMA_Handler,DMA_FLAG_TCIF3_7);
            HAL_UART_DMAStop(&UART1_Handler);      //传输完成以后关闭串口DMA
        }
        
        if(DBG_Flag==false)
        {
            memset(SendBuff,0,sizeof(SendBuff));
    //        printf("C:%sA ",array);
            myftoa(f_Current_A,array);//0.0001875 = 1/32768.0*6.144   //Current_A
            strcat(SendBuff,"C:");strcat(SendBuff,array);strcat(SendBuff,"A ");
            
    //        printf("V:%sV ",array);
            myftoa(f_Voltage_V,array);//0.000375 = 1/32768.0*6.144*2 //Voltage_V
            strcat(SendBuff,"V:");strcat(SendBuff,array);strcat(SendBuff,"V ");     
            
    //        printf("F:%sN ",array);
            myftoa(f_Force_N,array);//0.00004001667=0.000375/2*0.3*0.725925925926*0.98 //Force_N
            strcat(SendBuff,"F:");strcat(SendBuff,array);strcat(SendBuff,"N ");
            
    //        printf("L:%smm ",array);        
            myftoa(f_Laser_mm,array);//LaserOffset
            strcat(SendBuff,"L:");strcat(SendBuff,array);strcat(SendBuff,"mm ");
            
    //        printf("T0:%sS ",array);            
            myftoa(WaveCLK0,array);
            strcat(SendBuff,"T0:");strcat(SendBuff,array);strcat(SendBuff,"S ");
            
    //        printf("T1:%sS ",array);
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

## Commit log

2018-03-12 绘制完PCB
    [IPMC_MACP - ADC放错位置.PcbDoc, IPMC_MACP - 完成1.PcbDoc, IPMC_MACP - 完成1.SchDoc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]
2018-03-12 添加README
2018-03-12 README添加更新日志
2018-04-07 调通AD5722,ADS1115
    [IPMC_MACP - 修改.xlsx, IPMC_MACP.PcbDoc, IPMC_MACP.PrjPcb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]
2018-04-07 补充Readme
2018-04-10 上位机控制DA0的输出波形
    [IPMC_MACP.SchDoc, protocol.xlsx]
2018-04-23 完善PC发波形、fix
    [PN-Power.PcbDoc, PN-Power.PrjPcb, PN-Power.SchDoc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]
2018-04-26 test setting
    [IPMC_MACP.SchDoc]
2018-04-30 增加了CAN总线支持控制2个板子
    [protocol.xlsx]
2018-05-01 添加自动搜寻串口功能
2018-05-05 Add UCOS-II
    [IPMC_MACP.SchDoc]
2018-05-06 自动更新上位机
2018-05-11 通过manifest获取管理员权限
2018-05-11 修正了多次安装后在应用程序删除列表下出现多个一样应用的问题
2018-05-16 增加激光位移传感器和错误码
    [IPMC_MACP.SchDoc]
2018-05-19 电压校准、上位机界面修改、上位机快捷键支持
    [IPMC_MACP.SchDoc]
2018-05-19 电压校准、上位机界面修改、上位机快捷键支持,指示灯与错误码建立联系
2018-05-19 波形显示、上传更多数据、上传速率提高到20ms
2018-05-25 优化协议解析方案，未解决运行卡顿问题
2018-05-26 图表缓冲区。图表开关。采样时间。解决卡顿
2018-05-27 增加温湿度，及其上位机解析，遗留电流检测问题，上位机图表显示
2018-06-09 降低ADC采样速度，增加过流LED指示
    [IPMC_MACP.PrjPcb, IPMC_MACP.SchDoc, protocol.xlsx]
2018-07-06 增加双通道同时控制的支持
2018-07-09 修改协议，提高串口速率，提高采样率，修改检查更新文件
2018-07-14 提高采样率、串口速率、与机械臂通信等
    [0.1046.xlsx, 0.1198.xlsx, 0.25g.xlsx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]
2018-09-12 新增XY图、优化逻辑、新增一些功能开关
    [力标定数据与曲线.xlsx, 平台外壳.dwg, 新力.xlsx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]
2018-09-15 修改上位机界面风格
2019-03-02 添加PID控制、Bangbang控制
    [protocol.xlsx]
2019-03-05 重要修复、新增协议、逻辑优化
    [protocol.xlsx]
2019-03-08 上位机快捷键修改
2019-03-12 优化缩放功能、launch窗口居中、自定义控件、控件降级为17级
2019-03-16 新增pid等控制、界面优化降级、细节修复等[C
    [protocol.xlsx]
2019-04-04 增加tips提示框
2019-04-06 新增license，修改更新url，新增说明资料和tips框
    [protocol.xlsx]
2019-04-07 新增html使用手册
    [平台外壳.dwg]
2019-04-08 修改了上位机窗口显示标题
2019-04-08 细节优化
2019-04-08 整理结构。更换了一个图标
2019-04-12 区分了测控板和测控平台的定义
2019-04-12 新增看门狗，上位机新增电路原理图等资料
    [IPMC_MACP.PcbDoc, IPMC_MACP.SchDoc, bom.xlsx]
2019-04-13 删除无操作系统版本的程序
2019-04-18 新增flash子模块，新增BootLoader的上下位机代码
2019-04-18 新增copy.bat用于压缩和迁移源代码，上位机集成下位机源码[C
2019-04-28 忘记加了什么功能，好像完善了能量计量功能
    [protocol.xlsx]
2019-04-28 使用二次曲线标定力传感器数据，拟合相关性明显好于一次曲线，并做了一定滤波
2019-04-29 初步增加位移变化率闭环，但未验证
2019-05-04 修复一些问题,新增iir滤波器
2019-05-04 优化上位机结构，现在不那么容易卡顿了（不卡顿时间理论上延长10倍）
2019-05-06 新增清空XY图按键，优化使能控制按键逻辑
2019-05-06 新增清空XY图按键，优化使能控制按键逻辑，补充README文件
2019-05-09 新增更新控制参数按钮
2019-05-10 修改上位机细节；能量超过阈值前从恒压控制改为横功率控制
2019-05-13 增大曲线能够存储的点数，给XY图增加开关
    [protocol.xlsx]
2019-05-13 修改了功率控制算法，剔除不少深藏着的bug
2019-05-14 修复了算法的一些逻辑问题
2019-05-14 增加一个分隔显示波形图，完善control1和control2的功能，并移入选项卡
    [protocol.xlsx]
2019-05-15 进一步优化了算法细节，功率控制算法现在应该更完美了，可能没什么bug了
    [protocol.xlsx]
2019-05-15 完善功率控制算法，新增分隔显示曲线图，其他优化
2019-05-15 支持解析新版本更新信息
2019-05-16 修复了非2秒过渡时间下能量估计不准确的问题
2019-12-16 下位机增加过流后复位保护，由于低采样率下时间不准，暂时关闭采样率调整功能
2019-12-16 关闭采样率调节。增加过流时单片机自动复位保护
2020-01-09 修正手册中的错误
